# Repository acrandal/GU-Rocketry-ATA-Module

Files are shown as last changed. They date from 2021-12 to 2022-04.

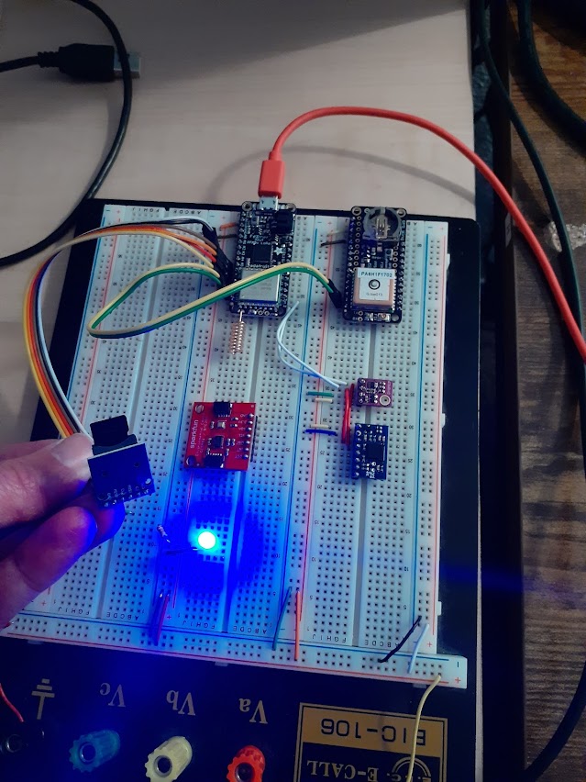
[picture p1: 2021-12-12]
Onboard/Images/Breadboard-Alpha-v01.jpg

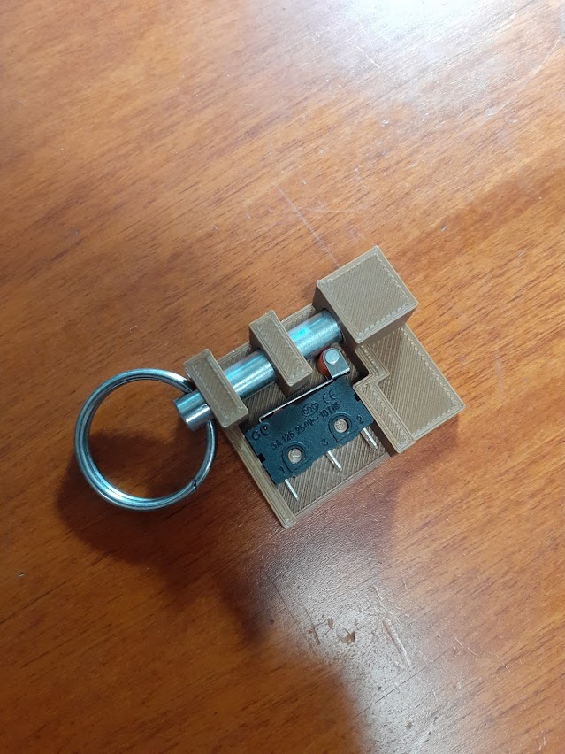
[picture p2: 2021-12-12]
Onboard/Images/PowerSwitch-Off.jpg

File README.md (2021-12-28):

# GU Rocketry ATA Module

ATA: Alternative To Aluminium

Gonzaga University ASME Rocketry Club  
2021-2022 Annual Competition Rocket  
Project for data collection of telemetry onboard

-----

## Devices / Data Sources

The system has several on board sensors and data sources.
These parts are all read for telemetry and environmental data during rocket operations.

### Environmental sensor: Sparkfun Environmental Combo  
https://www.sparkfun.com/products/14348

CCS811 Sensor
- Carbon Dioxide (CO2)
- Total Voltaic Compounds (TVOC)

BME280
- Temperature (C)
- Atmospheric Pressue (Pa)
- Altitude Estimate (m)
- Relative Humidity (%)

-----

### Message formatting

Data is stored on the onboard SD card and transmitted over the packet radio.
Both use the same shorthand format for saving space and bandwidth.

Environmental data packing:  
ENV: millis,CO2,TVOC,C,Pa,Alt(m),Humidity%

Contributors:
- Aaron S. Crandall \<crandall@gonzaga.edu>

Copyright: 2021  
License: GPL v3.0

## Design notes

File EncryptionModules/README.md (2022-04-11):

# Info on crypto module

The dependencies for the encryption system are not clear, but included here.
RadioHead uses the rweather crypto libraries for algorithms, but they're not in the Arduino standard release system 100%.

Libraries are found here:  
https://github.com/rweather/arduinolibs

We're using the CryptoLW/src/Speck.h implementation

Our crypto key is really stupid, but mostly for filtering interference more than actually protecting our data.

You also need to uncomment one line in the RadioHead.h source:  
#define RH\_ENABLE\_ENCRYPTION\_MODULE

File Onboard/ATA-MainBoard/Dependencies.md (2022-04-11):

# General Notes On Dependencies

Encryption requires several libraries & tweaks:

1 - RadioHead library
2 - Uncomment the "#define RH_ENABLE_ENCRYPTION_MODULE" in RadioHead.h source
3 - Encryption via the Speck.h implementation by rweather:  
  https://github.com/rweather/arduinolibs  
  Install the CryptoLW directory into your Arduino/libraries/ location  
  No, this isn't obvious and it's not part of the Arduino releases/libraries system

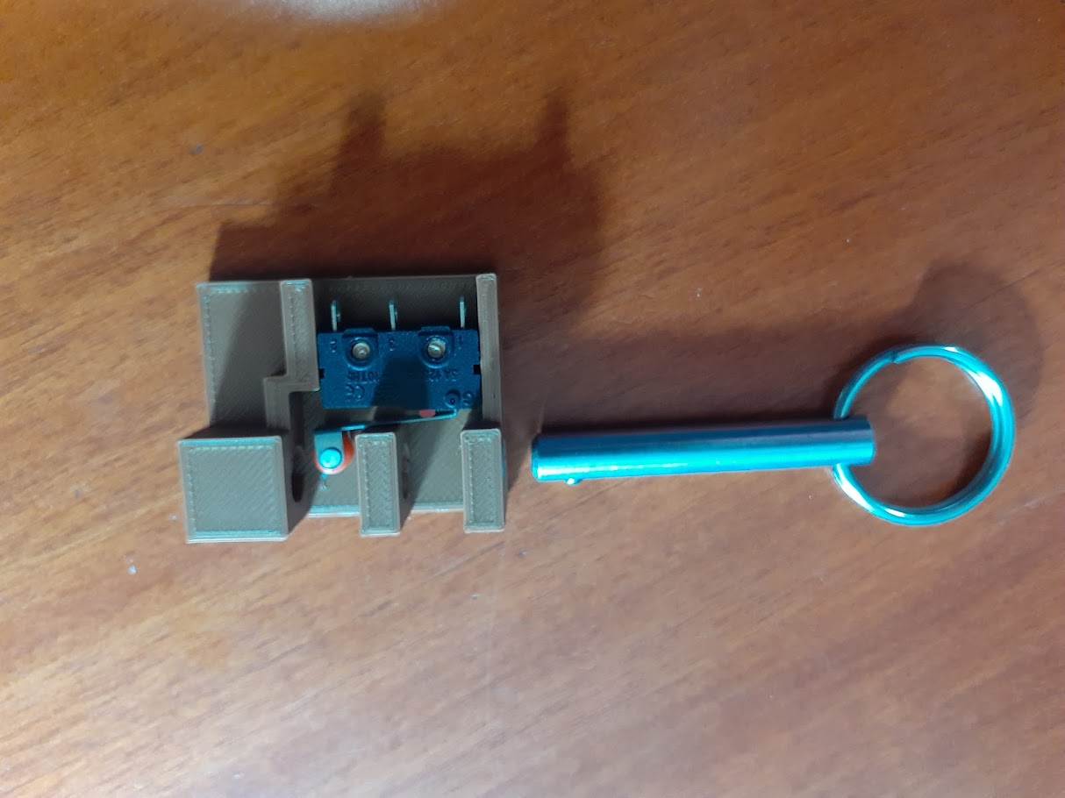
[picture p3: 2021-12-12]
Onboard/Images/PowerSwitch-Active.jpg

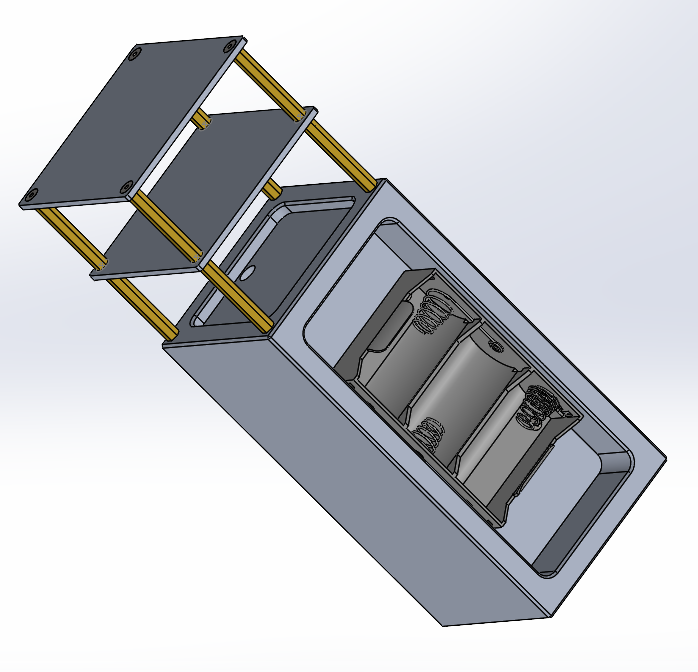
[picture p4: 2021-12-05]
Frame/FrameFullView.png

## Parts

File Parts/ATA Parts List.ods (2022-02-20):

Part | Qty | Cost | Total | URL
Adafruit Feather M0 with RFM95 LoRa Radio - 900MHz - RadioFruit | 1 | $34.95 | $34.95 | https://www.adafruit.com/product/3178 | Payload main processor/board
Adafruit Feather 32u4 RFM95 LoRa Radio- 868 or 915 MHz - RadioFruit | 1 | $34.95 | $34.95 | https://www.adafruit.com/product/3078
Adafruit Ultimate GPS FeatherWing | 1 | $24.95 | $24.95 | https://www.adafruit.com/product/3133
Adafruit 9-DOF Absolute Orientation IMU Fusion Breakout - BNO055 - STEMMA QT | 1 | $19.95 | $19.95 | https://www.adafruit.com/product/4646
Simple Spring Antenna - 915MHz | 2 | $0.95 | $1.90 | https://www.adafruit.com/product/4269
18650 battery holder V3 board compatible with Raspberry Pi Raspberry Pi 3 overcharge protection 5V 2 sections | 1 | $7.00 | $7.00 | https://bit.ly/3lHAAYB
Liitokala 100% New HG2 18650 3000mAh Rechargeable battery (2 batteries) | 1 | $7.50 | $7.50 | https://bit.ly/3rD9cPm
I2C SPI BMP280 5V Digital Barometric Pressure Altitude Sensor DC High Precision 1.8-5V Temperature Module | 1 | $2.70 | $2.70 | https://bit.ly/3pvKfmc
4pcs/lot 4x6 5x7 6x8 7x9 Double Side Prototype PCB Universal Printed Circuit Board Protoboard | 1 | $4.00 | $4.00 | https://bit.ly/3GnXD2L
Adafruit LoRa Radio Bonnet with OLED - RFM95W @ 915MHz - RadioFruit | 1 | $32.50 | $32.50 | https://www.adafruit.com/product/4074
Total |  |  | $170.40

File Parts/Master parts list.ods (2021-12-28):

Part | Qty | Price | Cost | Purpose | URL/Documentation
Adafruit Feather M0 with RFM95 LoRa Radio - 900MHz - RadioFruit | 1 | $34.95 | $34.95 | ATA Payload main processing board | https://www.adafruit.com/product/3178
Adafruit Ultimate GPS FeatherWing | 1 | $24.95 | $24.95 | Payload GPS sensor | https://www.adafruit.com/product/3133
Absolute Orientation IMU BNO055 | 1 | $5.70 | $5.70 | Inertial Measurement (IMU) Sensor | https://amzn.to/3dKIzQw
CCS811/BME280 (Qwiic) Environmental Combo | 1 | $35.95 | $35.95 | Co2 / Temp / Barometric Pressure / Humidity sensor | https://www.sparkfun.com/products/14348
Lithium Ion Battery Pack - 3.7V 4400mAh | 1 | $19.95 | $19.95 | ATA Payload main battery power | https://www.adafruit.com/product/354
Detent Quick Release Pin – 6.3mm diameter, 1 ½” length | 1 | $3.00 | $3.00 | Remove before flight power control pin | https://amzn.to/3IH4Eh1
Adafruit Feather 32u4 RFM95 LoRa Radio- 868 or 915 MHz - RadioFruit | 1 | $34.95 | $34.95 | Base station radio receiver | https://www.adafruit.com/product/3078
Limit Switch Roller Lever Arm SPDT | 1 | $0.25 | $0.25 | ATA Payload main power switch | https://bit.ly/3IHa2AL
Header Kit for Feather - 12-pin and 16-pin Female Header Set | 2 | $0.95 | $1.90 | Replaceable ATA MB feather parts | https://www.adafruit.com/product/2886
Right Angle 2 pin 2.54mm pitch JST headers | 2
JST connector 2 pin 2.54mm pitch (female) | 2
Protoboard 2.54mm pitch 8x12cm | 1
Totals |  |  | $161.60

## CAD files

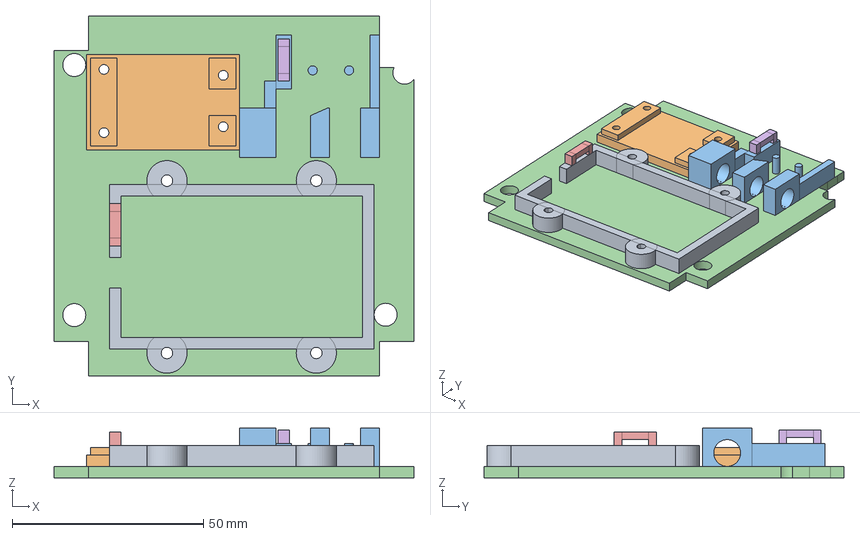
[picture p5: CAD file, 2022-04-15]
Frame/FullPowerModuleAssembly.FCStd
94.0 x 94.0 x 13.0 mm
Battery Backside
Regulator Base
Switch Pin - fitted
Backplate - with nut recesses
Battery Ziptie Ring
Main Power Ziptie Ring

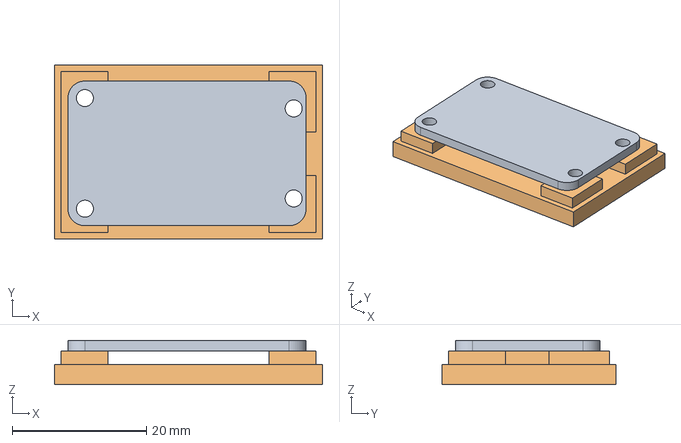
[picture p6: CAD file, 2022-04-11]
Frame/PowerRegulatorBase.FCStd
40.0 x 26.0 x 6.59 mm
Regulator Object
Regulator Base

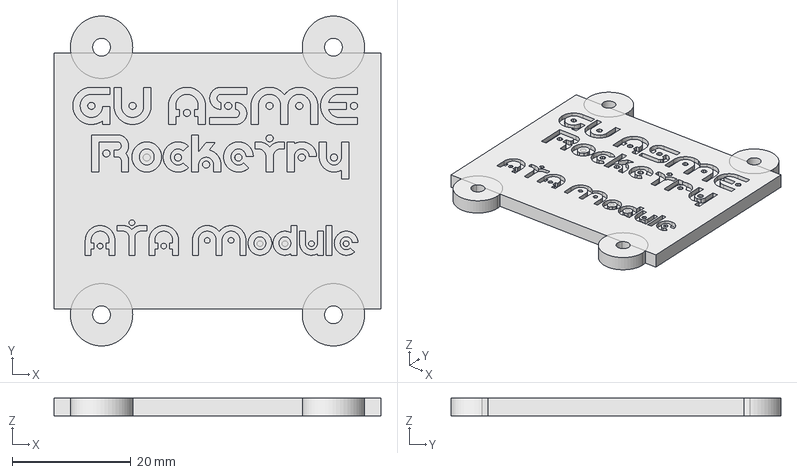
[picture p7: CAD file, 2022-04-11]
Frame/BatteryPlate.FCStd
55.0 x 55.5 x 3.00 mm

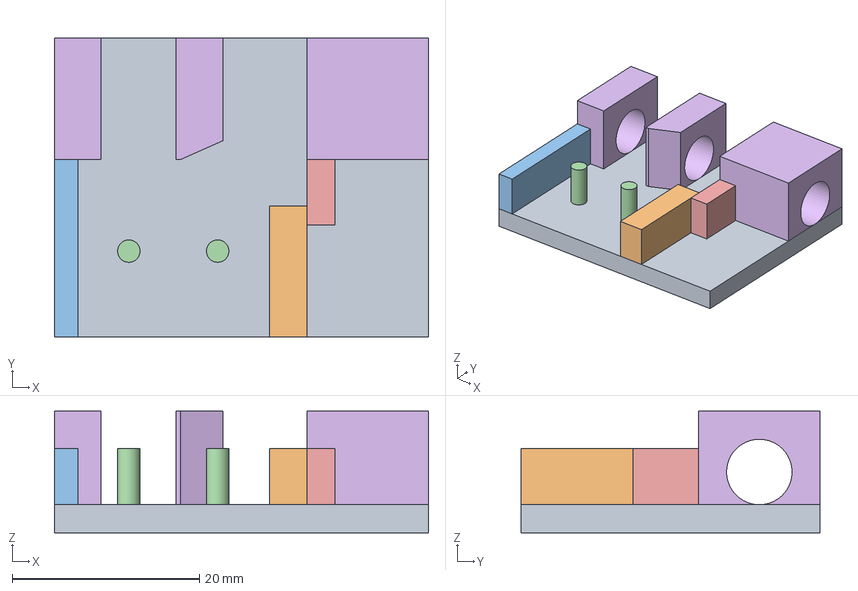
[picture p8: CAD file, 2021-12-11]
Frame/PowerPinFrame.FCStd
40.0 x 32.0 x 13.0 mm
Base Plate
Switch wall right
Switch wall left
Switch Pins
Dust cover block
Pin Blocks Holed

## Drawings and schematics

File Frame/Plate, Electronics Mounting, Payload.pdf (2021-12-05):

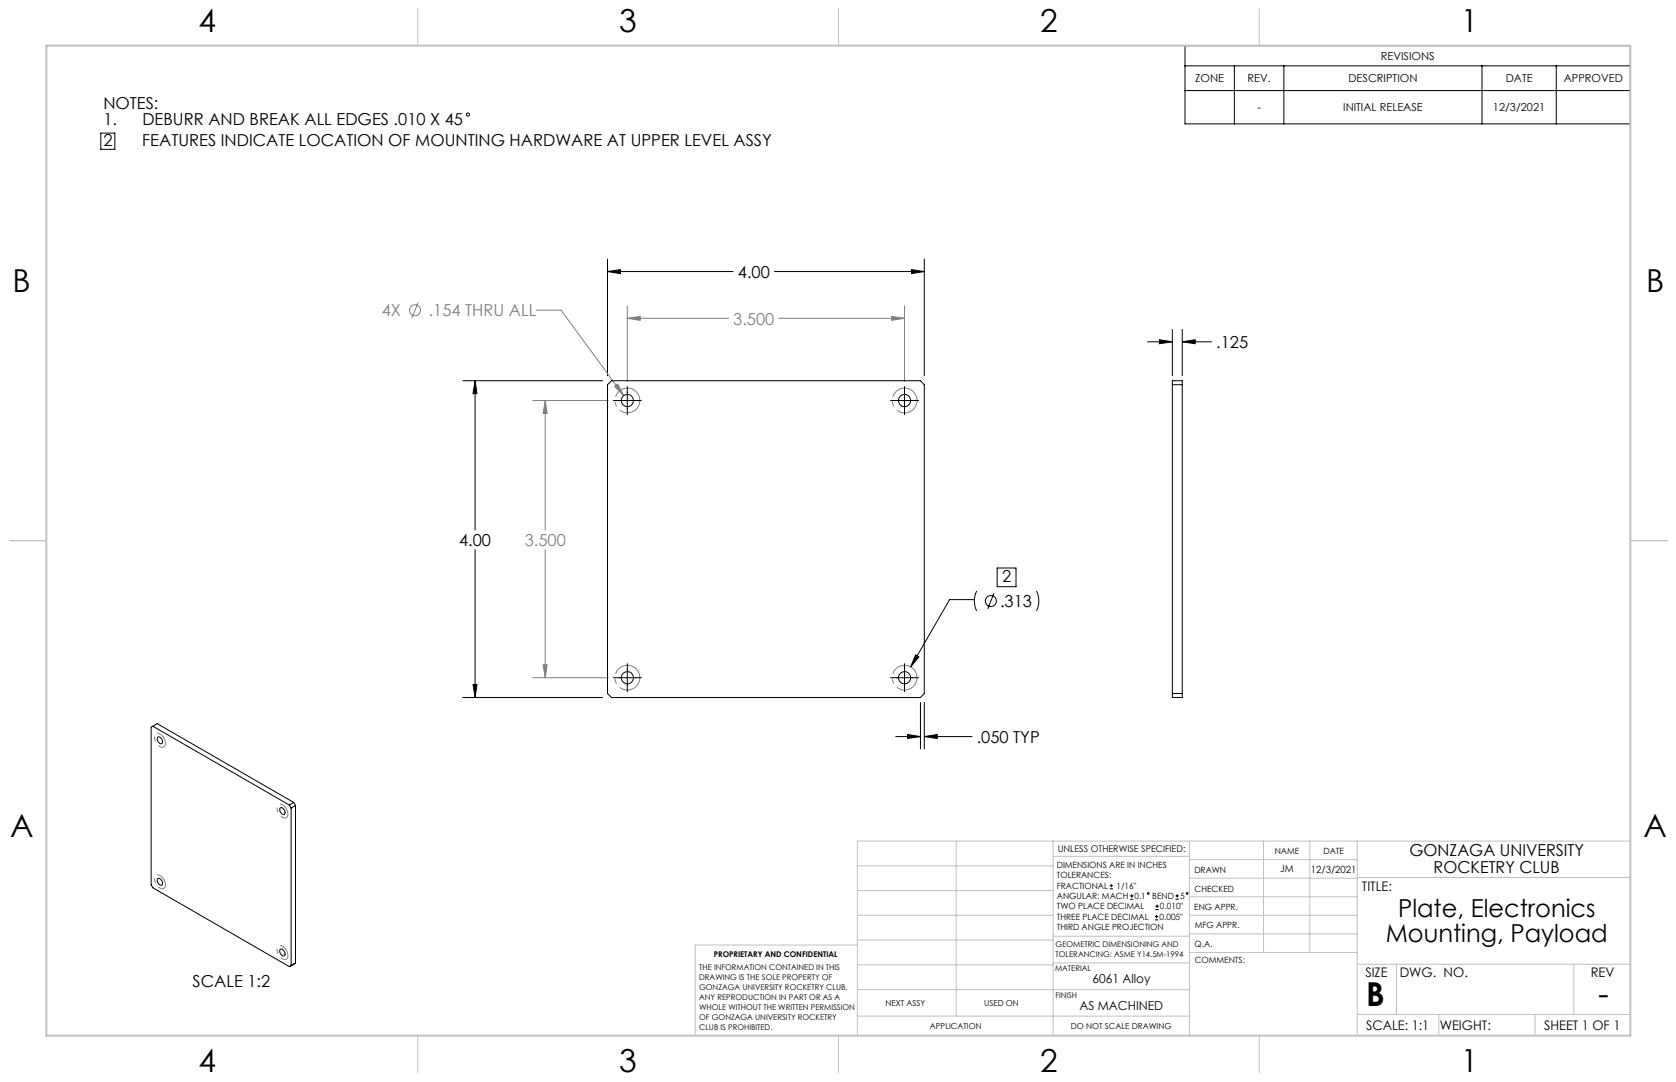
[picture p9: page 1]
.154 THRU ALL; .050 TYP; SCALE 1:2; FEATURES INDICATE LOCATION OF MOUNTING HARDWARE AT UPPER LEVEL ASSY

REVISIONS

ZONE | REV. | DESCRIPTION | DATE | APPROVED

NOTES:
1. DEBURR AND BREAK ALL EDGES .010 X 45

- | INITIAL RELEASE | 12/3/2021

UNLESS OTHERWISE SPECIFIED: | | NAME | DATE | GONZAGA UNIVERSITY ROCKETRY CLUB
DIMENSIONS ARE IN INCHES TOLERANCES: FRACTIONAL 1/16" ANGULAR: MACH 0.1 BEND 5 TWO PLACE DECIMAL 0.010" THREE PLACE DECIMAL 0.005" THIRD ANGLE PROJECTION | DRAWN | JM | 12/3/2021

CHECKED | | | TITLE: Plate, Electronics Mounting, Payload

ENG APPR.
MFG APPR.

GEOMETRIC DIMENSIONING AND TOLERANCING: ASME Y14.5M-1994 | Q.A.
MATERIAL 6061 Alloy | | SIZE B | DWG. NO. SHEET 1 OF 1 | REV - DO NOT SCALE DRAWING

PROPRIETARY AND CONFIDENTIAL
THE INFORMATION CONTAINED IN THIS
DRAWING IS THE SOLE PROPERTY OF
GONZAGA UNIVERSITY ROCKETRY CLUB.
ANY REPRODUCTION IN PART OR AS A
WHOLE WITHOUT THE WRITTEN PERMISSION
OF GONZAGA UNIVERSITY ROCKETRY
CLUB IS PROHIBITED.

NEXT ASSY | USED ON | AS MACHINED FINISH
APPLICATION | | | SCALE: 1:1 | WEIGHT:

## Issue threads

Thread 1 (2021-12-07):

SD card: Timestamps

acrandal, 2021-12-07:
Every X # of seconds (either 1 or 10 or so?) - snag the time from the GPS receiver (if it has one) and write it out as a unix epoch to the SD card so we know which "run" this is.

This avoids needing to do file rotation on the SD card.

The alternative is to only stamp the card once you have a GPS time? Not cool.... hrm. Maybe I should rotate anyway in addition to the timestamps?

Each line will get a millis() too.

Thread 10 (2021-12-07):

ANT: Would a larger antenna help on reception?

acrandal, 2021-12-07:
Current plan is just a spring antenna.

Would a larger dish or yagi antenna be more effective? They'd need to aim during the flight, especially the yagi.
It'd be fun to put a scope on a yagi and have someone try to track the rocket with it.

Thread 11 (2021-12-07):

PARTS: Need to order the Adafruit parts for the project.

acrandal, 2021-12-07:
Needs:

- Feather M0 RFM69 LoRa 900 MHz Board
- RFM69 LoRa 900 MHz Pi Bonnet
- Raspberry Pi 3 B+
- 2X SD cards

I should ask Paul first and then go to startup funds.

acrandal, 2021-12-11:
Requested Helena purchase the:
Feather M0 RFM69 LoRa 900 MHz Board

Ideally, it would arrive around Christmas time for work after the 1st.

acrandal, 2021-12-12:
I prototyped some with an Adalogger M0 board. So far all devices connect to it properly and there's a ton of code space. The SAMD 32 bit M0 core should do just fine.

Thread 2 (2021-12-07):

IMU: Get a BNO055 Demo working

acrandal, 2021-12-07:
Test out my BNO055 and get a demo file working on the feather

acrandal, 2021-12-07:
Turns out the BNO055 I got from China is wired to the I2C address 0x29.

acrandal, 2021-12-11:
The sensor is working just fine. Seems to have output on accel, gyro, gravity, mag, and orientation without issue. The temperature sensor works too.

Code for the demo is checked into the repo and I have photos of the board wired up, but it's all basics. No interrupts are needed, nor extra signal pins for configuration.

Closing.

Closed 2021-12-11.

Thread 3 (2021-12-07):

ENV: DEMO Barometric, Temperature, Humidity, Altitude

acrandal, 2021-12-07:
Get the BME280 sensor running. It's nice and small, plus the altitude estimates are very good, though offset based on sea level pressure that day.

acrandal, 2021-12-11:
This sensor worked fine. The code is in the repo with a small demo. I even did a quick hack to show it transmitting over the wireless link.

That said, the sensor will be replaced with the Sparkfun Environmental Combo which has a BME280 on board along with the IAQ sensor.

Closed 2021-12-11.

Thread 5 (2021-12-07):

GPS: Setup a demo / test

acrandal, 2021-12-07:
Get the GPS Ultimate Featherwing working over serial to the Feather.

- Pull down GPS
- Slim down the library API
- Evaluate the radio a bit (how long to a lock, etc)
- Put in a battery when it's time to really start testing seriously

acrandal, 2021-12-11:
GPS Featherwing board is working great. I've slimmed the demo to a bare minimum working version and shown that it's within about 12-20ft of ground truth on my desk. This is working great.

Closing.

Closed 2021-12-11.

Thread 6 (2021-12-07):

Power: Select some battery options

acrandal, 2021-12-07:
The power is still an unknown (just a bit):

- Try/choose between D cells, C cells, and 18650 cells.
- Must be able to run the ATA Payload for 2+ hours, with a 6 hour target
- Must be easily changeable or rechargeable

acrandal, 2021-12-07:
In any case, it has to be a very solid lock on the batteries so that during flight nothing shakes loose.
- this could mean fabricating a cap or hood if the case isn't already screwed shut.
- Batteries are going to go on the last facing away from the electronics.
- Needs to terminate with either a USB or JST connector to the board.
- Connectors need to be positive locking and firm

acrandal, 2021-12-07:
Did order some new 18650 cells and a 4 cell holder with USB charging for testing.

acrandal, 2021-12-07:
Need to get a large D cell holder for testing.
- D cells will need to work with some kind of power regulator (boost/buck) to ensure a steady 5v.

acrandal, 2021-12-12:
Currently trying a 4400 mAh LiIon pack from Adafruit. It plugs directly into the feather, provides enough runtime (we'll test it), and fits into the ATA Payload area easily.

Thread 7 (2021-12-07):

Power: Remove before flight key/pin - get one

acrandal, 2021-12-07:
Need to find a pin for the remove before flight power control assembly.

- Assembly will be 3d printed
- Holds dead man's switch internally
- Needs to hold the key with at least some level of friction to ensure safe travel to the assembly/pad location
    - Could use a little lever to clamp key? Not sure on this one - maybe mechEs can help :-)

acrandal, 2021-12-11:
The last pin that I purchased was from the hardware store. It was a pretty normal part at Ace. I'll track down another one.

acrandal, 2021-12-12:
I found a great pin in the switches box. It was the extra one from the ProtoSat project. I've designed and fabricated a remove before flight switch for it.

See: Frame/PowerPinFrame.FCStd

Closed 2021-12-12.

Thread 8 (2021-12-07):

IAQ: Air quality sensor demo

acrandal, 2021-12-07:
Test out the IAQ sensor we have in sparkfun environmental combo

- Just realized it also has a BME280 on board - could remove tiny external unit and replace with sparkfun unit entirely.

acrandal, 2021-12-07:
After looking at it, I think going entirely to the Sparkfun board would probably be for the best.

acrandal, 2021-12-11:
IAQ & BME280 combo board from Sparkfun:
- https://www.sparkfun.com/products/14348
- SparkFun Environmental Combo Breakout - CCS811/BME280 (Qwiic)

acrandal, 2021-12-28:
Combo works great, but for IAQ and BME features.

Closed 2021-12-28.

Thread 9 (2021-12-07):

Mounting: Find/cut a protoboard to fit footprint

acrandal, 2021-12-07:
In the end, we'll need two protoboards that fit on the ATA Frame Plates.

(Reminder: need to name the plates and/or sides of the plates)

They'll be on the order of 3.75 x 3.75" with corners milled out to clear the standoffs.

acrandal, 2021-12-12:
I found a couple of protoboard sheets that are more than big enough for the ATA footprint.

The best one is likely 80x120mm, which can be cut down to fit. That should provide enough sq mm of space for all of the electronics on the A side of the plate.

acrandal, 2021-12-12:
I'll open a new issue for the actual mounting stage later.

Closed 2021-12-12.

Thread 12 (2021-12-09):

Mounting: Need to snag the mounting plates from MTC

acrandal, 2021-12-09:
Jared milled the mounting plates and they're in the MTC for me to pick up.

I should snag those.

acrandal, 2021-12-28:
Snagged the mounting plates. Already completed some initial board sizing for the ATA Payload Motherboard (ATA PM).

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

Closed 2021-12-28.

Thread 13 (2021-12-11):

SD: Rotate data files on boot

acrandal, 2021-12-11:
When the ATA Payload boots, it needs to determine the filename for the next data log file. I could just keep appending to the same file, but I feel that using a different one each time will keep things easier to track when it comes time to process the data.

The current algorithm is that the data files are in the root of the SD card (no directories) and follow the 8.3 file format as:
ATA00000.dat

Each time the device boots, it reads the files one by one, incrementing a counter for the filename number. Once it hits a free number, it uses that for the current logfile. It then creates the log file, writes out a header and begins operations.

The code for the filename search is already in the repo and has been tested on the SD card. Given the number space, it can reboot 99999 times before running out of filenames.

acrandal, 2021-12-11:
Demo in repo works on hardware setup. Closing.

Closed 2021-12-11.

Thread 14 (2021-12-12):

Mounting: Battery case for 4400mAh battery

acrandal, 2021-12-12:
The 4400 mHr battery looks like it should be able to do the job, both for size and storage.
It needs a frame/case to bolt it down, though. I'll try to come up with something.

Best design would likely be a clamshell bolted down to the plate.

acrandal, 2021-12-28:
I've decided to pass this off to the mechanical team. They're going to need to do the physical mounting for the various parts anyway.

We might also need to be going to an external battery pack in the ATA power well they have in the design, pending final power checks on power longevity.

Closed 2021-12-28.

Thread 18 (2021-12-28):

DATA: Decide on data packing format

acrandal, 2021-12-28:
JSON is going to be too verbose for this project - especially in the data wireless transmission area

We'll need to make a smaller format that's still parsable. Could just by CSV with a leader ID field. IE:
BME,temp,humidity,pressure,altitude
IAQ,CO2,TVOC
GPS,FIX,LAT,LONG,TIME

Those can be easily unpacked after the fact.
I could also put a file on the SD card with the storage description for posterity.

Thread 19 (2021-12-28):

Setup arduinocli based build & upload for faster dev & test

acrandal, 2021-12-28:
Use arduinocli to build our scripts. This will allow us to use other IDEs than ArduinoIDE for the project, especially as the code base size increases to handle the various sensors on board.

https://www.arduino.cc/pro/cli

Closed 2021-12-28.

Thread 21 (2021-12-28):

BNO055 - acceleration full scale range settings

acrandal, 2021-12-28:
The default range on the accelerometer is 4g. If the rocket will exceed this, it'll rail and we'll lose data. We need to add an interface or other way to set the range bits to select 8g or 16g ranges.

https://cdn-shop.adafruit.com/datasheets/BST_BNO055_DS000_12.pdf

Settings are on the data sheet at:
4.4.2 - ACC_Config
Register: 0x08
Bits: [0..1]

The easiest approach is to just add to my IMU object a forceful update, though I really should sent a PR to Adafruit.

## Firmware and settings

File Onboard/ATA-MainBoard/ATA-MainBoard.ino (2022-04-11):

/**
 * Alternative To Aluminum (ATA) Main Board
 * 
 * Telemetry Payload for Gonzaga University's
 * ASME Rocketry competition rocket, 2021-2022
 * 
 * Collects inertial, environmental, and GPS data
 * Stores locally on an SD card
 * Transmits via RFM9x LoRa for real time visualization
 * 
 * Authors:
 *   Aaron S. Crandall <crandall@gonzaga.edu>
 *   
 * Copyright: 2021
 * License: GPL v3.0
 */
 
#include <TaskScheduler.h>

#include "ATA_StatusLight.h"
#include "ATA_BME280.h"
#include "ATA_IAQ.h"
#include "ATA_IMU.h"
#include "ATA_GPS.h"
#include "ATA_SD.h"
#include "ATA_RFM96.h"

#define TASK_IAQ_INTERVAL_MS 2000               // Min value 1000
#define TASK_BME_INTERVAL_MS 200
#define TASK_GPS_INTERVAL_MS 2000               // Min value 1000
#define TASK_IMU_INTERVAL_MS 50                 // Targeting 20 Hz
#define TASK_SD_FLUSH_INTERVAL_MS 5000          // Flush buffers
#define TASK_LED_HEARTBEAT_INTERVAL_MS 2000
#define TASK_STATUS_LIGHT_OFF_DELAY_MS 60000    // 1 Minute

// Top defines for operational tasks
Scheduler taskScheduler;

// Forward definitions for taskScheduler callback functions
void ataIAQ_TaskCallback();
void ataBME280_TaskCallback();
void ataGPS_TaskCallback();
void ataIMU_TaskCallback();
void ataSDFlush_TaskCallback();
void ataLEDHeartbeatBlink_TaskCallback();
void ataStatusLightOff_TaskCallback();

// Task Scheduler task definitions for various tasks
Task taskIAQ(TASK_IAQ_INTERVAL_MS, TASK_FOREVER, &ataIAQ_TaskCallback, &taskScheduler, true);
Task taskBME280(TASK_BME_INTERVAL_MS, TASK_FOREVER, &ataBME280_TaskCallback, &taskScheduler, true);
Task taskGPS(TASK_GPS_INTERVAL_MS, TASK_FOREVER, &ataGPS_TaskCallback, &taskScheduler, true);
Task taskIMU(TASK_IMU_INTERVAL_MS, TASK_FOREVER, &ataIMU_TaskCallback, &taskScheduler, true);
Task taskSDFlush(TASK_SD_FLUSH_INTERVAL_MS, TASK_FOREVER, &ataSDFlush_TaskCallback, &taskScheduler, true);
Task taskLEDHeartbeat(TASK_LED_HEARTBEAT_INTERVAL_MS, TASK_FOREVER, &ataLEDHeartbeatBlink_TaskCallback, &taskScheduler, true);
Task taskStatusLightOff(TASK_STATUS_LIGHT_OFF_DELAY_MS, TASK_ONCE, &ataStatusLightOff_TaskCallback, &taskScheduler, false);

// Setup hardware driver handles/objects
ATA_StatusLight statusLight = ATA_StatusLight();
ATA_BME280 ata_bme280 = ATA_BME280();
ATA_IAQ ata_iaq = ATA_IAQ();
ATA_IMU ata_imu = ATA_IMU();
ATA_GPS ata_gps = ATA_GPS();
ATA_SD ata_sd = ATA_SD();
ATA_RFM96 ata_rfm96 = ATA_RFM96();

// General string buffer for data reads
char buf[120];

// Tracking current onboard LED heartbeat light status
bool lightBlinkOn = true;

// Setup the various sensors and SD card hardware
void initializeDevices() {
    int checkingDelay = 200;
    int bootingDelay = 100;

    statusLight.setChecking(); delay(checkingDelay);
    ata_rfm96.begin();          // Setup packet radio
    statusLight.setBooting(); delay(bootingDelay);

    statusLight.setChecking(); delay(checkingDelay);
    ata_bme280.begin();         // Barmometric pressure / altitude init
    statusLight.setBooting(); delay(bootingDelay);

    statusLight.setChecking(); delay(checkingDelay);
    ata_iaq.begin();            // Indoor air quality sensor init
    statusLight.setBooting(); delay(bootingDelay);

    statusLight.setChecking(); delay(checkingDelay);
    ata_imu.begin();            // Motion sensor (accel/gyro) initialized
    statusLight.setBooting(); delay(bootingDelay);

    statusLight.setChecking(); delay(checkingDelay);
    ata_gps.begin();            // GPS radio initialized
    statusLight.setBooting(); delay(bootingDelay);

    statusLight.setChecking(); delay(checkingDelay);
    ata_sd.begin();             // Initialize SD card for onboard logging
    statusLight.setBooting(); delay(bootingDelay);
}

// ** ************************************************************************
void setup() {
    pinMode(LED_BUILTIN, OUTPUT);

    Serial.begin(115200);       // Initialize the serial port

    statusLight.begin();        // Initialize the RGB LED status light
    statusLight.setBooting();   // Show user that we're booting the board

    delay(3000);                // Delay to let serial port settle & user to connect

    initializeDevices();        // Initialize sensors and hardware

    // ata_env.enableVerbose();
    // ata_gps.enableVerbose();
    // ata_imu.enableVerbose();

    // Set status light to system boot results
    if( !ata_sd.isNominal() ) {
        statusLight.setErrorSD();   // SD card failed - wireless, but no data storage
    }
    else {
        statusLight.setNominal();   // We're running nominally, let the user know
    }

    // Initialize taskScheduler
    taskScheduler.startNow();   // Set task scheduling system to start from now (millis())
    taskStatusLightOff.enableDelayed();    // Start countdown to set status light off

    Serial.println(F("ATA MainBoard initialized - beginning operations."));
}


// ** ************************************************************************
void loop() {
    // Check the task event queue
    taskScheduler.execute();
    //delay(10);  // Tiny "polite" delay
}

// TaskScheduler callback functions/tasks
void ataIAQ_TaskCallback() {
    ata_iaq.getValues(buf);
    ata_rfm96.sendAsync(buf);
    ata_sd.println(buf);
}

void ataBME280_TaskCallback() {
    ata_bme280.getValues(buf);
    ata_rfm96.sendAsync(buf);
    ata_sd.println(buf);
}

void ataGPS_TaskCallback() {
    ata_gps.getValues(buf);
    ata_rfm96.sendAsync(buf);
    ata_sd.println(buf);
}

void ataIMU_TaskCallback() {
    ata_imu.getValues(buf);
    // ata_rfm96.sendAsync(buf);
    ata_sd.println(buf);
}
 
void ataSDFlush_TaskCallback() {
    // Serial.println("Flushing SD buffers");
    ata_sd.flush();
}

void ataLEDHeartbeatBlink_TaskCallback() {
    if(lightBlinkOn) {
        digitalWrite(LED_BUILTIN, HIGH);
        lightBlinkOn = false;
    } else {
        digitalWrite(LED_BUILTIN, LOW);
        lightBlinkOn = true;
    }
}

// Runs once @ after a while to turn off the status light
//  This saves a lot of power during flight
void ataStatusLightOff_TaskCallback() {
    statusLight.setOff();
}

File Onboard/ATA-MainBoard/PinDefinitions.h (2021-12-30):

/**
 * Hardware pinouts and other hardware setup
 */

#ifndef __PIN_DEFINITIONS_H
#define __PIN_DEFINITIONS_H

#define STATUS_LIGHT_PIN 5
#define STATUS_STRIP_LENGTH 1

#define ATA_SD_CHIP_SELECT_PIN A5

#define ATA_SD_WRITE_ENABLE_PIN 6

#endif

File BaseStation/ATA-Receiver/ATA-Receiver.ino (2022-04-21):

/*
 * ATA Receiver Bridge
 * 
 * Alternative To Aluminum (ATA) Telemetry & Environment Payload
 * 
 * Gonzaga University ASME Rocketry Club
 *   2021 competition rocket payload
 * 
 * @author Aaron S. Crandall <crandall@gonzaga.edu>
 * @copyright 2021
 * @license GPL v3
 * 
 * Hardware:
 *  Adafruit Feather M0 LoRa Radio (RFM9x) -- https://www.adafruit.com/product/3179
 *  433 MHz spring antenna
 */

#include <SPI.h>
#include <RH_RF95.h>              // RadioHead Arduino RF library
#include <RHEncryptedDriver.h>    // RadioHead encryption shim / encoder / decoder
#include <Speck.h>                // Speck encryption library - https://rweather.github.io/arduinolibs/classSpeck.html


// Pin settings for Feather 32u4 board
/*
#define RFM95_CS 8
#define RFM95_RST 4
#define RFM95_INT 7
*/

// Pin settings for Feather M0 RFM9x board
#define RFM95_CS 8
#define RFM95_RST 4
#define RFM95_INT 3


// #define RF95_FREQ 915.0
#define RF95_FREQ 434.0     // currently set for some 400 MHz M0 boards


// Create RFM API object
RH_RF95 rf95(RFM95_CS, RFM95_INT);

// Setup encryption
// See RadioHead rf95_encrypted_client.pde
//  Uses https://github.com/rweather/arduinolibs/tree/master/libraries/CryptoLW
Speck speckCipher;   // Instanciate a Speck block ciphering
RHEncryptedDriver rf95EncryptedDriver(rf95, speckCipher); // Instantiate the driver with those two

//unsigned char encryptkey[16] = {1,2,3,4,5,6,7,8,9,10,11,12,13,14,15,16}; // The very secret key

// Key is ASCII: "GUASMEROCKETRY!!"
unsigned char encryptkey[16] = {71, 85, 65, 83, 77, 69, 82, 79, 67, 75, 69, 84, 82, 89, 33, 33};

char msg[255];


// ** *************************************************************************
void setup()
{
  pinMode(LED_BUILTIN, OUTPUT);
  pinMode(RFM95_RST, OUTPUT);
  digitalWrite(RFM95_RST, HIGH);

  Serial.begin(115200);
  while (!Serial) {
    delay(1);
  }
  delay(100);

  Serial.println("DAT: {\"MSG\":\"ATA Receiver Bridge Booting\"}");

  // manual reset
  digitalWrite(RFM95_RST, LOW);
  delay(10);
  digitalWrite(RFM95_RST, HIGH);
  delay(10);

  while (!rf95.init()) {
    Serial.println("DAT: {\"MSG\":\"ATA Receiver Bridge Booting\"}");

    Serial.println("ERR: {\"MSG\":\"LoRa radio init failed\"}");
    //Serial.println("Uncomment '#define SERIAL_DEBUG' in RH_RF95.cpp for detailed debug info");
    while (1);
  }
  Serial.println("DAT: {\"MSG\":\"LoRa radio init OK!\"}");

  // Setting cipher's key
  Serial.println("DAT: {\"MSG\":\"Setting crypto key\"}");
  speckCipher.setKey(encryptkey, sizeof(encryptkey));

  // Defaults after init are 434.0MHz, modulation GFSK_Rb250Fd250, +13dbM
  if (!rf95.setFrequency(RF95_FREQ)) {
    Serial.println("ERR: {\"MSG\":\"setFrequency failed\"}");
    while (1);
  }

  sprintf(msg, "DAT: {\"MSG\":\"Set Freq to: %s\"}", String(RF95_FREQ, 2).c_str());
  Serial.println(msg);

  rf95.setTxPower(23, false);

  Serial.println(F("DAT: {\"MSG\":\"ATA Receiver Bridge Booted- Beginning operations\"}"));
}


// *************************************************************************************************
// ** Check if radio has data & print it out to Serial
void handleRF95Receive() {
  if( rf95.available() )
  {
    uint8_t buf[RH_RF95_MAX_MESSAGE_LEN];  // Max is 250 bytes
    uint8_t len = sizeof(buf);

    if( rf95EncryptedDriver.recv(buf, &len) )
    {
      digitalWrite(LED_BUILTIN, HIGH);
      
      buf[len] = '\0';  // Null terminate the string with # bytes copied

      // Emit string without altering, just put a DAT: lead for parsing/errors
      // Serial.print("DAT: ");
      Serial.print("RCV: ");
      Serial.println((char*)buf);

      // Also emit the RSSI of the received packet as JSON
      //Serial.print("DAT: {\"RSSI\": ");
      Serial.print("RCV: RSSI: ");
      Serial.println(rf95.lastRssi(), DEC);
      //Serial.println("}");

      digitalWrite(LED_BUILTIN, LOW);
    }
    else
    {
      Serial.println("ERR: Receive failed");
    }
  }
}

// ** Serial echo/command handler
void handleSerialReceive() {
  Serial.setTimeout(20);      // Check for bytes REALLY FAST (we don't care what they are)
  if(Serial.available() > 0) {
    Serial.println("DAT: {\"ID\": \"ATA-Receiver\"}");
    String dataRead = Serial.readString();  // Empty buffer for next loop
    //Serial.println(dataRead);
  }
  Serial.setTimeout(1000);    // Reset to default timeout - prevents programming interrupt troubles
}


// ** **********************************************************************************
void loop()
{
  handleRF95Receive();        // Check radio, print if data
  handleSerialReceive();      // Check for incoming serial in buffer - echo/control
}

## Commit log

2021-12-05 Initial ATA receiver RFM bridge arduino code
2021-12-11 Updated Adafruit BME280 code for Sparkfun board I2C address
    [PowerPinFrame.FCStd]
2021-12-12 First images of system development - power switch and breadboarding
2021-12-12 Simple IAQ testing script for CCS811 Co2 sensor
2021-12-13 Initial master parts list sheet started
    [Master parts list.ods]
2021-12-28 Updated parts list for latest design
    [Master parts list.ods]
2021-12-28 Converted testing code to use 434.0 M0 radios for Issue #16 (#17)
    [ATA-Receiver.ino, ATA-Transmitter.ino]
2021-12-28 Setup ArduinoCLI build & deploy toolchain (#20)
    * Initial demo of a blink sketch using arduinocli functional
    * Added ignore for CAD temp files
    * Initial mainboard arduino file created. uses ArduinoCLI to build & deploy. Initial StatusLight class for status LED interface
2021-12-28 Environmental Sensor Package wrapper initial version constructed
2021-12-28 Added millis() to ENV output string
2021-12-28 Initial stub in of IMG/BNO055 sensor
2021-12-28 IMU initial object functional wrapper in place.
2022-02-20 Starting Task based data polling
    [ATA Parts List.ods]
2022-04-05 millis proper output fixes
2022-04-05 Starting to frame in base station data replay mockup tool
2022-04-09 Working test of split IMU, more configuration clarity on device polling. Makefile added more aliases to targets
2022-04-11 Power system modules mounts FreeCAD done
    [BatteryPlate.FCStd, PowerRegulatorBase.FCStd]
2022-04-11 Initial full power module 3D model
    [FullPowerModuleAssembly.FCStd]
2022-04-11 Ver 1.0 of full power module frame mount and datasets included
    [BatteryPlate.FCStd, PowerRegulatorBase.FCStd]
2022-04-11 Google Earth kml file generator and example data framed in
2022-04-15 Added ziptie rings and battery cushion
    [FullPowerModuleAssembly.FCStd]
2022-04-21 Added some current receiver output for parsing tests
2022-07-26 Added some datasets for testing and course materials
2022-07-27 Added two more motorcycle trips
2022-07-28 A couple more motorcycle datasets
